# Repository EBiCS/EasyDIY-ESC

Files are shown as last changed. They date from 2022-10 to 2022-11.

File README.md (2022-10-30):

# EasyDIY ESC

Note: 'main' branch is under development, there is a change to use KiCad as compared to v0.5.2 (current HEAD of feature/v0_5_2, i.e. git SHA1 - e55e314)

The target for this EV motor controller is to power small EVs like EBikes or EScooters like Xiaomi M365, and offer better customizability and repairability.

## Main objectives:

* **Easy to build and repair DIY**: It uses DC-DC modules, a development board instead of an uC chip, SMD passive components are all 0805 or bigger, and ICs are SOIC8 or SOIC14. No fine pitch components.

* **Popular components:** Uses the popular Bluepill STM32F103 board, meaning it is easy to develop firmware for it. Uses popular components / footprints / pinouts. Meaning you should have no problems with part availability, and if you do, you will be able to change most parts with equivalents depending on availability or prefrence, without need to change the pcb layout.

* **Possible to add custom electronics:** For reusing this motor controller on different devices, you can extend the electrocnis with a custom header on top of the Bluepill. This means you can use all available pins and access and extend with: CAN, UARTs, etc.

* **Possibility to buy the SMD parts pre-soldered:** While we went to great extend do make this board easy to DIY by humans (as opposed to robots in a factory), we acknowledge there are many who lack the skill/time/motivation to solder all SMDs themselves. So all SMDs are on the same side, in large stock at lcsc (at the time of writing), so the board can be ordered with SMDs pre-assembled by JLCPCB for a decent price.

* **Compactness:** Despite using only big DIY friendly parts, we tried to keep the board as small as possible: ~ 73mm x 49mm

* **Good Power/Size ratio:** Our initial estimation (untested) is that the upper limit for phase current should be ~78A. As for max continuous “battery amps”, it heavily depends on the cooling!  

## ES Thread:
https://endless-sphere.com/forums/viewtopic.php?f=30&t=114537

## Building Tips:

### **Bus Bars**
Bus bars are recommended for anything else than very low current. (extra copper wires soldered to the exposed copper strips of the PCB, or at very least a lot of solder on the exposed strips)

### **Bulk electrolytic capacitors (XC.... )**
We went for a total of ~1000uF, which should be enough for most usecases. 
You need more capacitance the more power you plan to use, and the longer (and thinner) your battery wires are. So you can probably also get away with less if you have short thick battery wires.  
Choose voltage rating ~ 1.5x your max battery voltage for a long lifetime. For 48v nominal (54.6V max) battery voltage, 80V or more is recommended. 
The total capacitance of the electrolytic capacitors is more important than the exact combination of values. 1 big + 3 small is almost the same as 3 medium of the same total value. More smaller capacitors have the advantage of lower ESR, lower inductance, and redundancy in case one fails)

### **Bulk ceramic/MLC capacitors:  (XC.... )**
As much as possible. These need to compensate for the high frequency weakness of the electrolytic capacitors. Overrating voltage rating is recommended. (author chose 100V for the “default” for 3.3v, 5v and 12v). Definitely fill all open footprints. 

### **Capacitors - the rest**
Values are consolidated for easy buying. Voltage rating is 25V or higher regardless if they are on the 12v, 5v, or 3v3 rail on the default design, however you can choose a smaller voltage rating for the 5v and 3v3 rails..  
All parts are 0805 mlc (2 electrolytic exceptions, C8 and C10 from the 12v and 5v rails)

### **Snubbers (RSx, CSx)**
These are RC snubbers. **The current values for the R and C are random, they are here only for the footprints. Do not fit them (yet).** The real values (if necessary at all) will be computed after we build the controller and see what ringing we get. Purpose of the snubbers is to dampen that ringing. (if you choose different parts than the one we compute the snubbers for, you might need to compute the snubbers yourself). These components are not present in the pick-and-place or BOM files.

### **Optional Capacitors (OCx)**
All parts marked OCx are optional GS Capacitors for the mosfets. If you insist on using old/bad mosfets with high Crss, you'll need to compensate for that with additional Cgs. That being said, please avoid high Crss mosfets, and you don't need to use the OCx. We expect none of the recommended FETs to need these. These are footprints only to offer flexibility if needed. These components are not present in the pick-and-place or BOM files. 

### **FETs**
The default FETs are available from aliexpress at the time of writing. They are cheap and have good specs. (low Rds on, low Crss, 100v, etc). 
You can solder them “standing” on the the throughhole/module side, or bent flat on the opposite (smd) side. In either case, it is recommended that the thick part of the leads is in contact with (soldered to) the board. The thin part of the leads can carry significantly less current.

You can use a fet of your choosing, but please be aware that old Fets (such as the famous 4110 or 3077) have huge Crss, leading to a tiny Ciss/Crss ratio. This ratio needs to be bigger than roughly your max battery voltage, so you will need to compute and add the optional Cgs capacitors (OCx). Small Ciss/Crss results in ringing / parastic turn on (which leads to failure). 
That being said, it’s best to just use Fets with Ciss/Crss > ~100, nowadays they’re easy to find. See the spreadsheet with alternative parts. 

Attaching the FETs to a heatsink: the FETs need to be electrically isolated from the heatsink, but well connected thermally. The options for this are:
* Mica glass (“traditional option”, cheap, easy to find)
* Ceramics (saw this as a new option, never tried it)
* Polymer pads 
* Kapton Tape 

Unfortunately in focusing on making the board small we crammed the FETs very close together. This means some mica or ceramic pads will not fit - and it’s very hard to cut them afaik. So for this version we’re probably stuck with polymer / kapton. 

### **Testing**

* v0.5 build has been tested by mxlemming with MESC FOC firmware on F401CC black pill board

### **Known issues/limitations:**
* Mosfet temp sensor missing - you can add it to the expansion board. 
* Many connectors are not present (example: CAN)  - you can add them to the expansion board. 

## FAQ

* **What’s with those 2 solder jumpers?**
They are power for your uart-connected board. If it’s a 5v board, solder the 5v solder jumper, if it needs 3.3v solder the 3v3 jumper. Never solder both! 

* **Can you assemble it for me?**
You can get the SMD side pre-assembled at jlcpcb (at the time of design all parts were in stock for jlcpcb SMT service). So you’ll only need to solder the through-hole parts and the modules. Currently there is no plan on selling any assembled PCBs.

* **I want more power!!!**
This might not go well. So good luck, you’ll probably need it. Please don't blame us when it goes up in smoke. But do let us know how it goes. Disclamer aside, here are some basic suggestions:
   * Stack another 1mohm shunt on top of the other. This will double the max current you can read. 
   * Add thick bus bars to the board.
   * Add more/ bigger bulk caps!
   * Use appropriate wires (thick!) 

* **I want more voltage!!!!**
Realistic limit is 15s lipo. For more than that the ESC will need serious redesign.
Some bottlenecks that cross my mind: 
   * default 12v dc module is 72v limited, 
   * some of the recommended mosfets are not capable of more voltage, 
   * voltage sense divider needs adjustment, etc. 
   * PS: I would have loved to make it 20s capable, but did not find any small 100-12v DC-DC module. If you know of one, please let us know in our ES thread, and next version might be 20s / 74v capable. Also, I added 3 through hole pads for easy mounting of any 12V module via wires :)

* **Your part X is bad, I recommend Y!**
We tried to find cheap but decent parts for this controller. Cheap almost always implies a compromise in some other areas, so you might not like our pick :)
It should be fairly easy to switch to other parts on your own: we used mostly standard and popular footprints and packages
If you know better parts or have better solutions, please let us know on our ES thread. We like learning new things. 
....except if you’re going to suggest 3077 or 4110 mosfets. Those things are dinosaurs. They were the biggest baddest thing around during their time, but nowadays belong to a museum. Or a kid’s t-shirt. Please stop recommending them. See our thread for details.

* **Where can I buy parts?**
Lcsc.com, mouser.com. Aliexpress if needed. 
I designed this with jlcpcb smt assembly in mind, so all SMDs were in stock at lcsc when I designed the PCB. Also most of the Through-hole parts. 
Some exceptions, and where to buy them:
   * Default mosfets - aliexpress. 
   * 12v module - mouser
   * 5v module - aliexpress. There is a fixed voltage one, we recommend that one! 
   * Bluepill - aliexpress. Don’t know a better source these days. 
   * Jst headers - aliexpress
   * Bluepill headers - aliexpress

* **Why do the battery wires go in seemingly random places in the middle of the board?**
If you have the battery wires at the edge, then the full battery current will need to go through a portion of the battery “traces” of the PCB. I’ve placed them near the middle switch node, so with a tiny exception, the current through the traces is ⅓ of the battery current. 

* **This whole thing is amateur work!**
Yeah, totally true. We are amateurs working on a generic low power ESC for free. If by this you refer to any specific mistake / set of mistakes, we would love to know about it! Post in the ES thread. Thanks!

## Change log v0.5 -> v0.5.2

### Schematic
* Changes:
  * changed voltage sense resistors to 10x lower value (basic jlcpcb resistors -> cheaper)
  * removed pin 20 from GND (for blackpill compatibility)
  * removed thermal reliefs
  * replaced some parts with more cost-effective equivalents (basic parts jlcpcb)
  * changed diodes to a bigger more rugged version (more inline with the philosophy of this controller)
  * changed voltage sense divider so max read voltage is 100V (20s compatibility)
  * added circuitry for a ntc temp sensor for mosfets.
  * changed the electrolytic caps from the 12V and 5V rails to MLCC (still more capacitance than manufacturer recommends)
  * swapped ntc pins: MOSFET Temp -> A0, and Motor Temp -> A1 (for compatibility with EBiCS v2)
  * changed pinout of HALL JST connector - now you can use, additionally to a 6 pin connector for motors with temp NTC sensor, a 5pin connector on pins 1-5 and it will directly be compatible with the cable of a motor without temp sensor (M365 would be a popular example)
### PCB Design 
  * added 3 through hole pads for vbat, 12v, and gnd for easy connection with wires of any dc-dc module for more flexibility
  * moved JST connectors away from bluepill for better fitting (increased board width by 1mm)
  * many minor layout changes 

## Change log v0.1 -> v0.5

### Schematic
* Fixes:
  * added voltage divider for the voltage follower op-amp
  * added connection between the 3 2k2 resistors and 3V3 on hall sensor inputs
  * changed decoupling caps of the 3 power stages from VBAT-Shunt to VBAT-GND 

* Changes
  * replaced "default" mosfets with much better model
  * replaced shunts with 1mOhm (much lower value)
  * connected bluepill pin 20 to GND
  * changed the RC from the phase wire of the power stages to snubbers
  * replaced opamp with better model
  * changed Opamp 2 to be the voltage follower for easier routing
  * replaced vattery connectors with 2 pads for wire soldering
  * removed one of the connectors for hall sensors, replaced the other one with JST PH. 
  * pinout changes for leaving CAN pins free
  * replaced mini 360 with MP1584EN (is bigger, but there is a non-adjustable 5V version, which is less error-prone to use.)
  * changed all ceramic decoupling capacitors for 3v3 and 5v to 10uF 0805
  * changed all bootstrap capacitors to  10uF 0805
  * added 1 ceramic decoupling capacitor per power stage (for a total of 2) 
  * increased gain of opamps to 10 (from 8)
  * consolidated pullup R values to 2k2
  * consolidated many other C and R values
  * removed diode and cap from the hall sensor 5v rail
  * removed extension board headers (will be mounted on top of the bluepill on the same pins)
  * replaced electrolytic caps with bigger values and bigger voltage ratings

### PCB design:

* Fixes: 
  * Moved the decoupling capacitor close to the bus bars (GND was through a long thin trace which rendered it almost useless) 	

* Changes:
  * moved to 4 layer board (Ground Planes rule!)
  * moved the opamp non-inverting input resistors near the shunt - so they get the potential of that local ground (not of the GND near the opamp) 
  * stacked DC-DC modules
  * removed expansion board headers
  * added 3 JST PH headers for basic functions
  * moved vbat rail at the edge of the board and GND rail in the middle
  * major redesign of everything
  * greatly reduced the size

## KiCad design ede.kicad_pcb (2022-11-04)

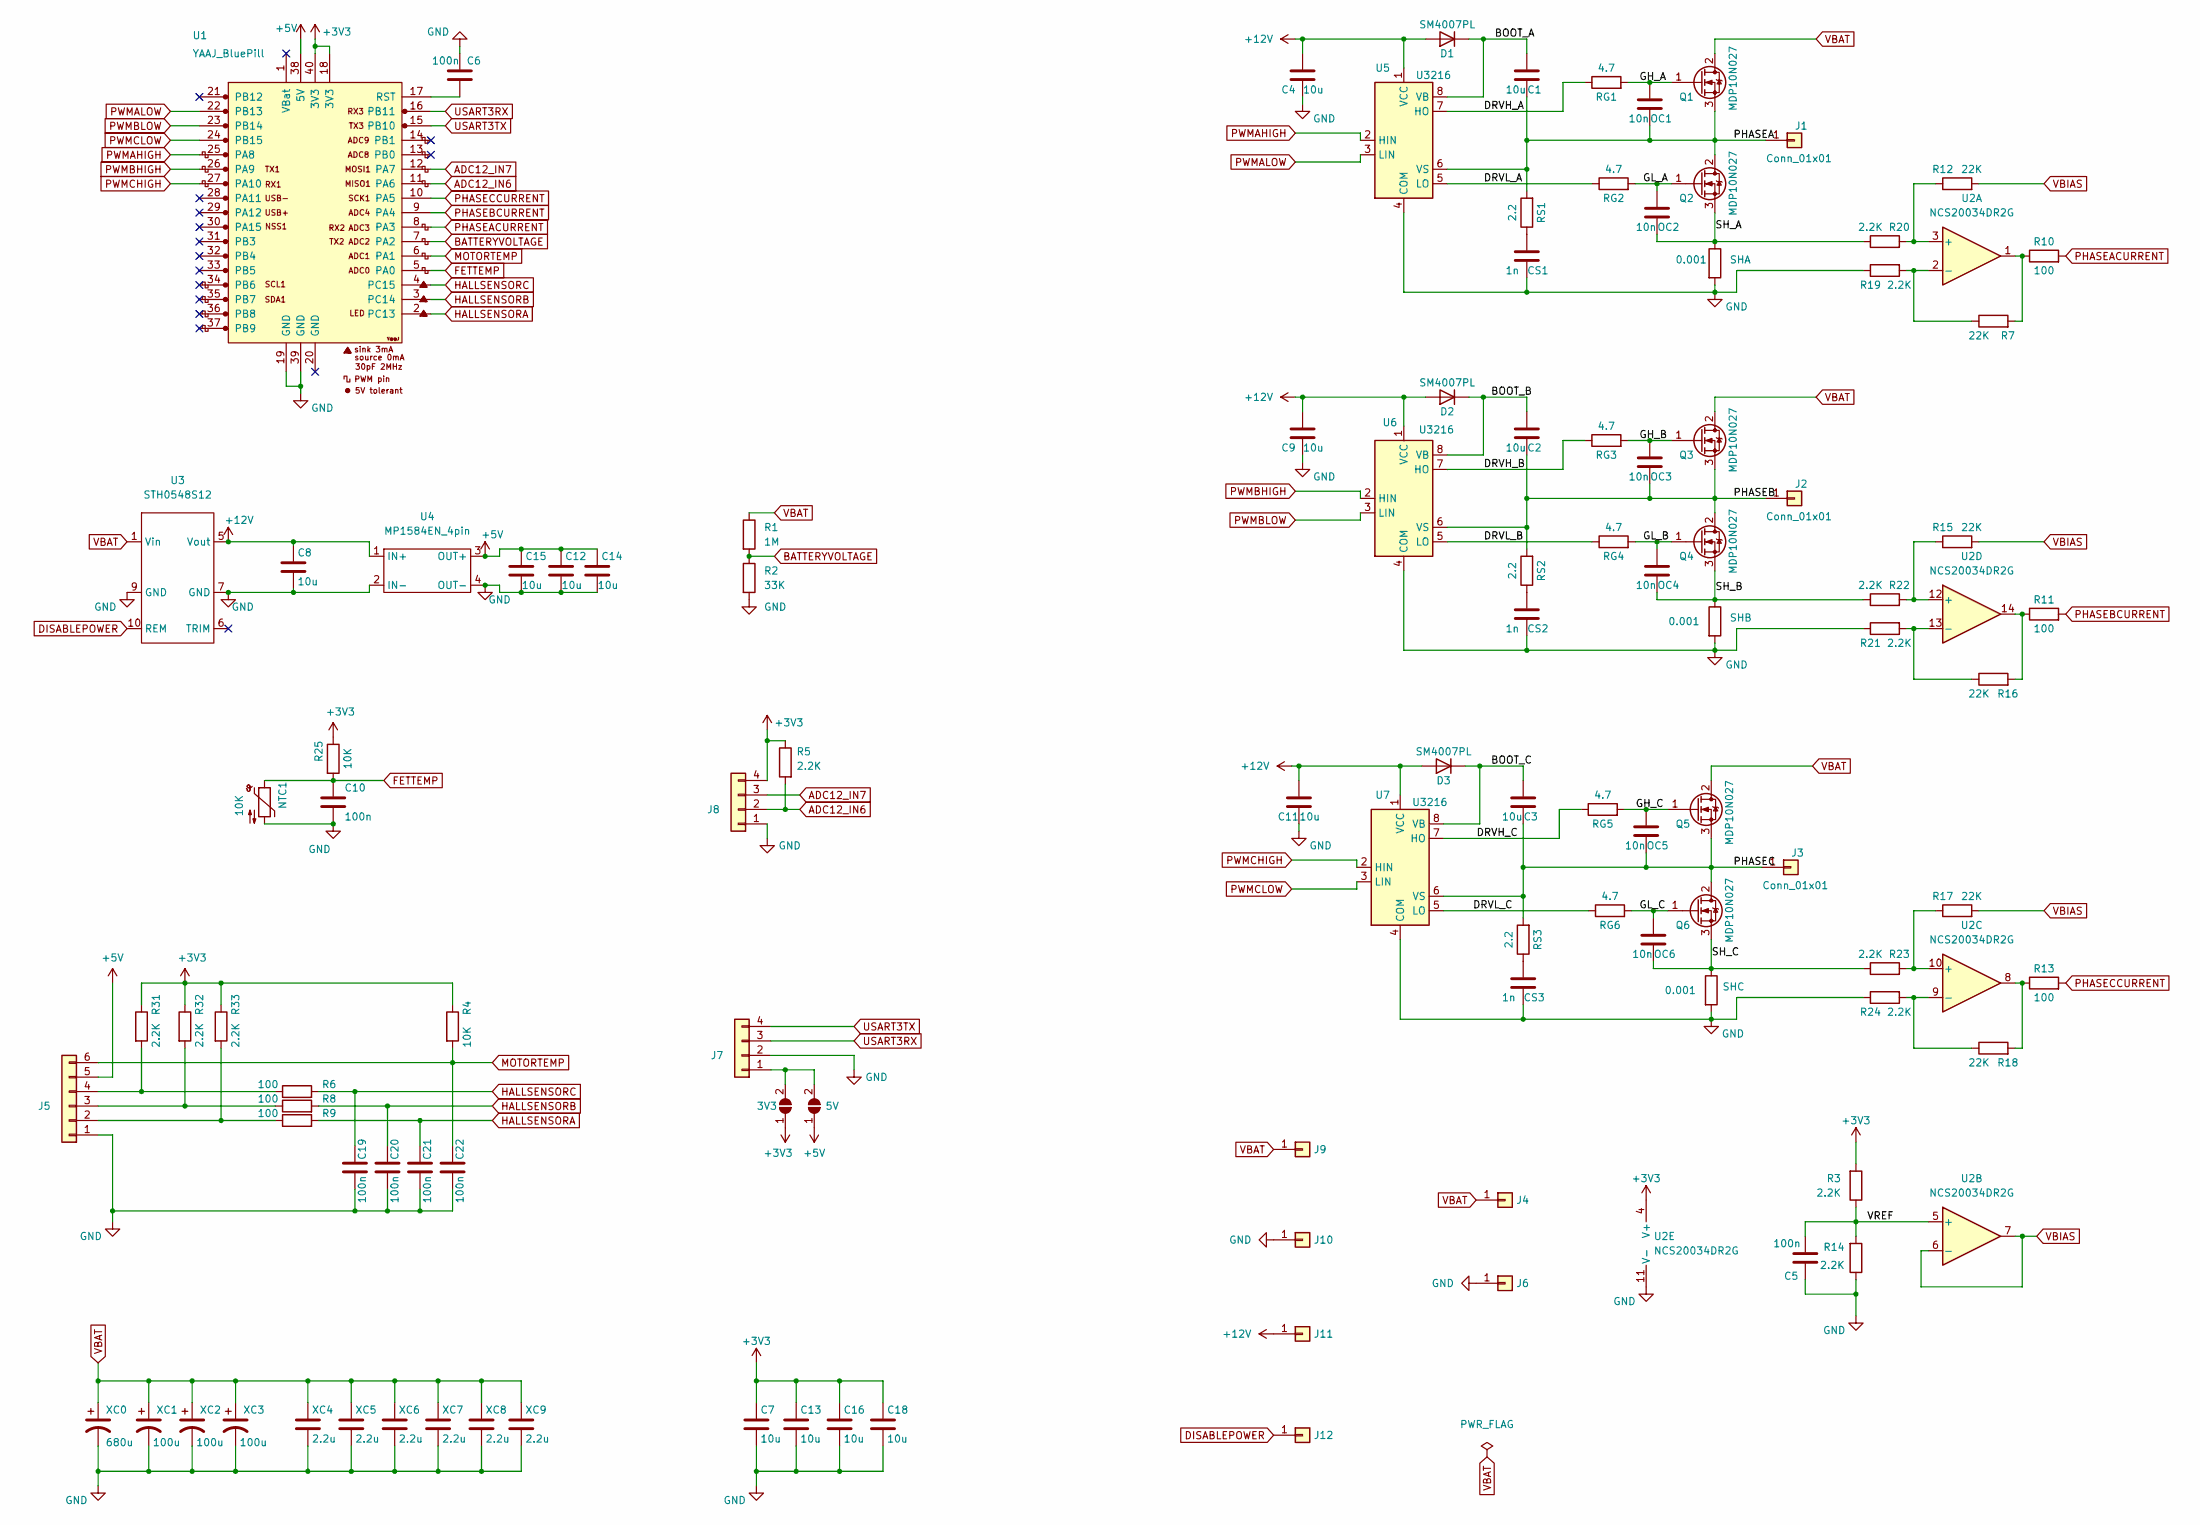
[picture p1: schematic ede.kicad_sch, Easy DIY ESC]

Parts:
C1, C2, C3, C4, C7, C8, C9, C11, C12, C13, C14, C15, C16, C18: 10u; C_0805_2012Metric_EDE
C5, C6, C10, C19, C20, C21, C22: 100n; C_0805_2012Metric_EDE
CS1, CS2, CS3: 1n; C_0805_2012Metric_EDE
D1, D2, D3: SM4007PL; D_SOD-123_EDE
J1, J2, J3, J4, J6: Conn_01x01; THT_1x_ID_2.8_OD_4
J5: Conn_01x06; JST_PH_B6B-PH-K_1x06_P2.00mm_Vertical_EDE
J7, J8: Conn_01x04; JST_PH_B4B-PH-K_1x04_P2.00mm_Vertical_EDE
J9, J10, J11: Conn_01x01; THT_1x_ID_1_OD_2
J12: Conn_01x01; TestPoint_Pad_D1.4mm_EDE
JP1, JP2: SolderJumper_2_Open; SolderJumper-2_small_EDE
NTC1: 10K; THT_2x_P2.54_ID_0.7_OD_1.3
OC1, OC2, OC3, OC4, OC5, OC6: 10n; C_0805_2012Metric_EDE
Q1, Q2, Q3, Q4, Q5, Q6: MDP10N027; TO-220-3_Vertical_EDE
R1: 1M; R_0805_2012Metric_EDE
R2: 33K; R_0805_2012Metric_EDE
R3, R5, R14, R19, R20, R21, R22, R23, R24, R31, R32, R33: 2.2K; R_0805_2012Metric_EDE
R4, R25: 10K; R_0805_2012Metric_EDE
R6, R8, R9, R10, R11, R13: 100; R_0805_2012Metric_EDE
R7, R12, R15, R16, R17, R18: 22K; R_0805_2012Metric_EDE
RG1, RG2, RG3, RG4, RG5, RG6: 4.7; R_0805_2012Metric_EDE
RS1, RS2, RS3: 2.2; R_0805_2012Metric_EDE
SH1, SH2, SH3: 0.001; R_2512_6332Metric_EDE
U1: YAAJ_BluePill; YAAJ_Bluepill
U2: NCS20034DR2G; SOIC-14_3.9x8.7mm_P1.27mm_EDE
U3: STH0548S12
U4: MP1584EN_4pin
U5, U6, U7: U3216; SOIC-8_3.9x4.9mm_P1.27mm_EDE
XC0: 680u; CP_Radial_D12.5mm_P5.00mm_EDE
XC1, XC2, XC3: 100u; CP_Radial_D8.0mm_P3.50mm_EDE
XC4, XC5, XC6, XC7, XC8, XC9: 2.2u; C_1206_3216Metric_EDE

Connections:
+3V3: C7.1, C13.1, C16.1, C18.1, J8.4, JP1.1 (A), R3.2, R4.1, R5.1, R25.1, R31.1, R32.1, R33.1, U1.18 (3V3), U1.40 (3V3), U2.4 (V+)
+5V: C12.1, C14.1, C15.1, J5.5, JP2.1 (A), U1.38 (5V), U4.3 (OUT+)
+12V: C4.1, C8.1, C9.1, C11.1, D1.2 (A), D2.2 (A), D3.2 (A), J11.1, U3.5 (Vout), U4.1 (IN+), U5.1 (VCC), U6.1 (VCC), U7.1 (VCC)
/BOOT_A: C1.1, D1.1 (K), U5.8 (VB)
/BOOT_B: C2.1, D2.1 (K), U6.8 (VB)
/BOOT_C: C3.1, D3.1 (K), U7.8 (VB)
/DRVH_A: RG1.1, U5.7 (HO)
/DRVH_B: RG3.1, U6.7 (HO)
/DRVH_C: RG5.1, U7.7 (HO)
/DRVL_A: RG2.1, U5.5 (LO)
/DRVL_B: RG4.1, U6.5 (LO)
/DRVL_C: RG6.1, U7.5 (LO)
/GH_A: OC1.1, Q1.1 (G), RG1.2
/GH_B: OC3.1, Q3.1 (G), RG3.2
/GH_C: OC5.1, Q5.1 (G), RG5.2
/GL_A: OC2.1, Q2.1 (G), RG2.2
/GL_B: OC4.1, Q4.1 (G), RG4.2
/GL_C: OC6.1, Q6.1 (G), RG6.2
/PHASEA: C1.2, J1.1, OC1.2, Q1.3 (S), Q2.2 (D), RS1.2, U5.6 (VS)
/PHASEB: C2.2, J2.1, OC3.2, Q3.3 (S), Q4.2 (D), RS2.2, U6.6 (VS)
/PHASEC: C3.2, J3.1, OC5.2, Q5.3 (S), Q6.2 (D), RS3.2, U7.6 (VS)
/SH_A: OC2.2, Q2.3 (S), R20.1, SH1.1
/SH_B: OC4.2, Q4.3 (S), R22.1, SH2.1
/SH_C: OC6.2, Q6.3 (S), R23.1, SH3.1
/VREF: C5.2, R3.1, R14.2, U2.5 (+)
ADC12_IN6: J8.2, R5.2, U1.11 (PA6)
ADC12_IN7: J8.3, U1.12 (PA7)
BATTERYVOLTAGE: R1.2, R2.1, U1.7 (PA2)
DISABLEPOWER: J12.1, U3.10 (REM)
FETTEMP: C10.1, NTC1.1, R25.2, U1.5 (PA0)
GND: C4.2, C5.1, C6.2, C7.2, C8.2, C9.2, C10.2, C11.2, C12.2, C13.2, C14.2, C15.2, C16.2, C18.2, C19.2, C20.2, C21.2, C22.2, CS1.2, CS2.2, CS3.2, J5.1, J6.1, J7.2, J8.1, J10.1, NTC1.2, R2.2, R14.1, R19.1, R21.1, R24.1, SH1.2, SH2.2, SH3.2, U1.19 (GND), U1.39 (GND), U2.11 (V-), U3.7 (GND), U3.9 (GND), U4.2 (IN-), U4.4 (OUT-), U5.4 (COM), U6.4 (COM), U7.4 (COM), XC0.2, XC1.2, XC2.2, XC3.2, XC4.2, XC5.2, XC6.2, XC7.2, XC8.2, XC9.2
HALLSENSORA: C21.1, R9.2, U1.2 (PC13)
HALLSENSORB: C20.1, R8.2, U1.3 (PC14)
HALLSENSORC: C19.1, R6.2, U1.4 (PC15)
MOTORTEMP: C22.1, J5.6, R4.2, U1.6 (PA1)
unnamed: C6.1, U1.17 (RST)
unnamed: CS1.1, RS1.1
unnamed: CS2.1, RS2.1
unnamed: CS3.1, RS3.1
unnamed: J5.2, R9.1, R33.2
unnamed: J5.3, R8.1, R32.2
unnamed: J5.4, R6.1, R31.2
unnamed: J7.1, JP1.2 (B), JP2.2 (B)
unnamed: R7.2, R10.1, U2.1
unnamed: R11.1, R16.2, U2.14
unnamed: R12.1, R20.2, U2.3 (+)
unnamed: R13.1, R18.2, U2.8
unnamed: R15.1, R22.2, U2.12 (+)
unnamed: R16.1, R21.2, U2.13 (-)
unnamed: R17.1, R23.2, U2.10 (+)
unnamed: R18.1, R24.2, U2.9 (-)
unnamed: R7.1, R19.2, U2.2 (-)
PHASEACURRENT: R10.2, U1.8 (PA3)
PHASEBCURRENT: R11.2, U1.9 (PA4)
PHASECCURRENT: R13.2, U1.10 (PA5)
PWMAHIGH: U1.25 (PA8), U5.2 (HIN)
PWMALOW: U1.22 (PB13), U5.3 (LIN)
PWMBHIGH: U1.26 (PA9), U6.2 (HIN)
PWMBLOW: U1.23 (PB14), U6.3 (LIN)
PWMCHIGH: U1.27 (PA10), U7.2 (HIN)
PWMCLOW: U1.24 (PB15), U7.3 (LIN)
USART3RX: J7.3, U1.16 (PB11)
USART3TX: J7.4, U1.15 (PB10)
VBAT: J4.1, J9.1, Q1.2 (D), Q3.2 (D), Q5.2 (D), R1.1, U3.1 (Vin), XC0.1, XC1.1, XC2.1, XC3.1, XC4.1, XC5.1, XC6.1, XC7.1, XC8.1, XC9.1
VBIAS: R12.2, R15.2, R17.2, U2.6 (-), U2.7

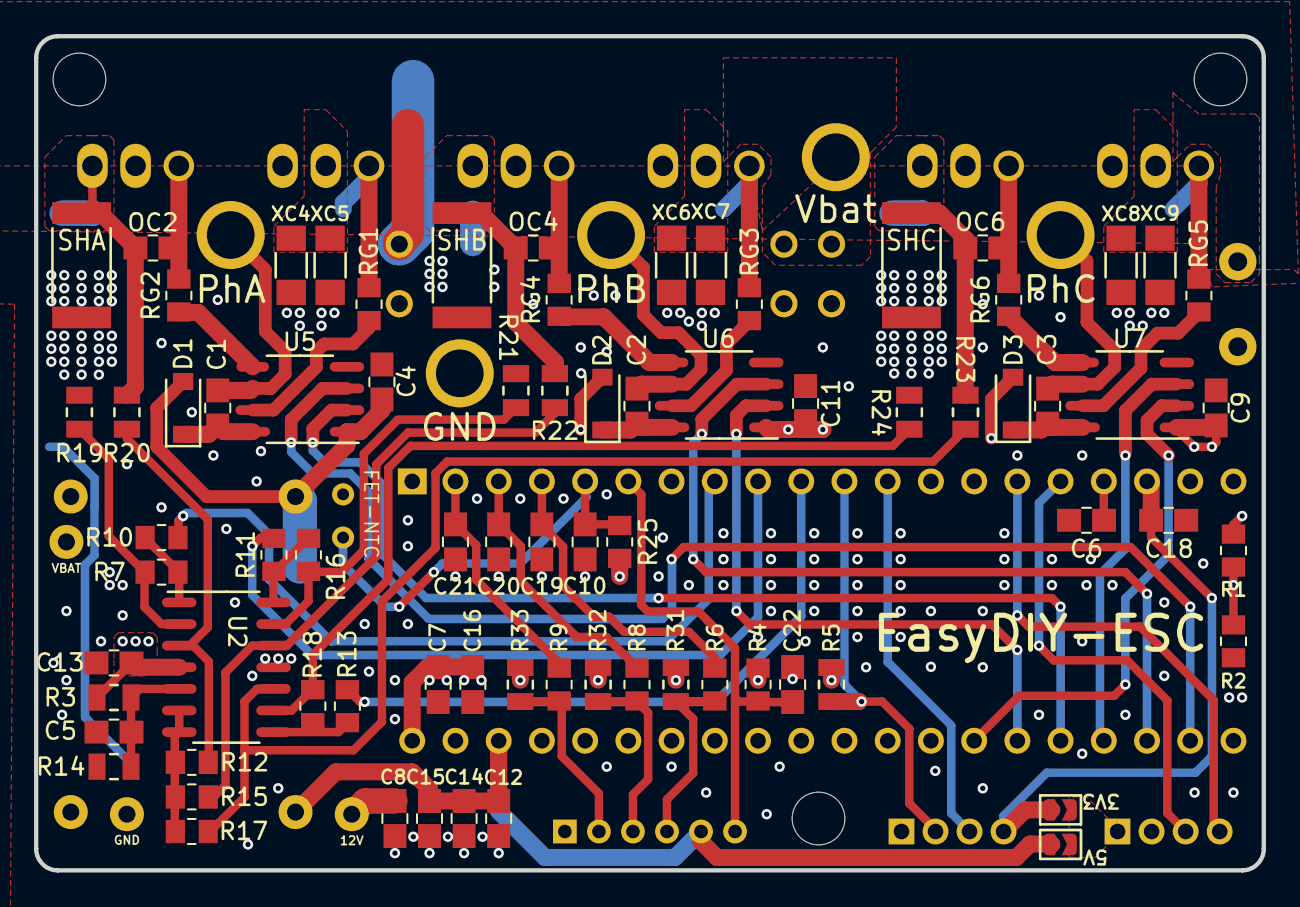
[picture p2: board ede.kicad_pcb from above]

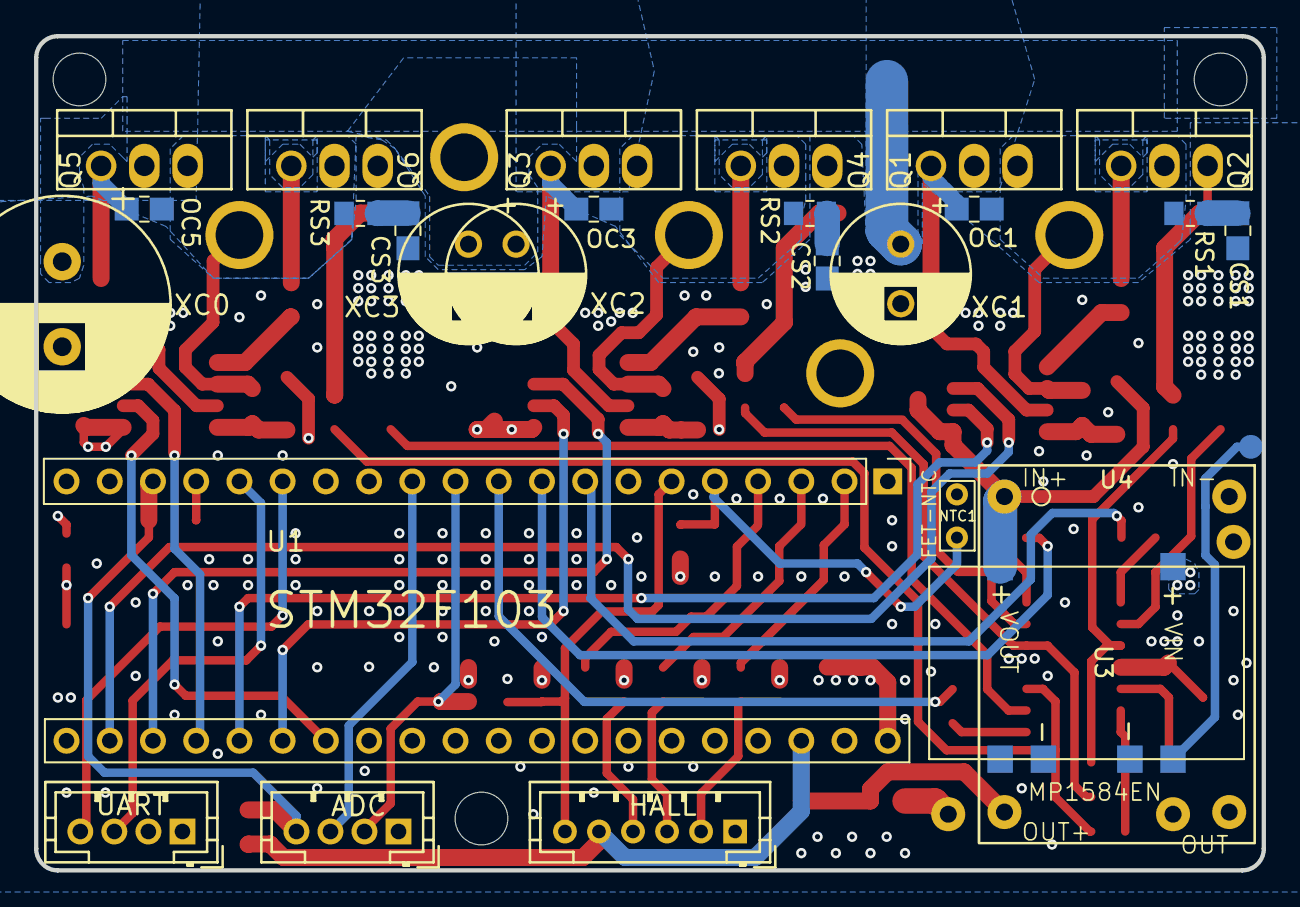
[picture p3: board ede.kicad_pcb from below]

Board: 4 copper layers, 72.1 x 49.0 mm, 111 parts (27 on the bottom side), 65 nets.

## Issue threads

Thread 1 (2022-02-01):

Two motors with one STM32 microcontroller?

happytm, 2022-02-01:
Is it possible to run 2 motors with one STM32 micro controller by adding 6 more mosfets?
Are there enough pin available?

Thanks.

runger1101001, 2022-02-01:
Yes, it is possible!

- If you want 2 x 6-PWM control you need a model with two advanced control timers, normally TIM1 and TIM8.
- It has to be a fairly fast MCU to run 2 times the SimpleFOC loop
- if you want current sensing, you will need 6 ADC pins also
- and you need 2 sensor inputs, for ABI you would ideally use 2 more timers and our [STM32HardwareEncoder](https://github.com/simplefoc/Arduino-FOC-drivers/tree/master/src/encoders/stm32hwencoder) or use SPI, maybe with two separate SPI buses...

I think most of the STM32G4 series would be suitable.

Here is an example design I made, with 2x 6-PWM, 2x current sensing and 2x SPI bus for sensors:
https://github.com/rosmo-robot/Rosmo_ESC

runger1101001, 2022-02-01:
(but it is not possible using a BluePill or BlackPill MCU board - not enough pins; but I guess one of the big Nucleo boards could do it...)

happytm, 2022-02-03:
Thank you @runger1101001 for your insight.

happytm, 2022-02-08:
@runger1101001 How about using ESP32 ? Does it have enough pins to run 2 motors?

Thanks.

runger1101001, 2022-02-08:
Pins are always in short supply on the ESP32! It only has relatively few to begin with compared to other MCUs, and then they are so complicated to use... some are input only, some can't be used at the same time as WiFi, and some are only "pretend" pins since they're actually connected to the flash memory can you can't use them at all...

So the answer is: it depends.
A DevKit type MCU-board: not really, I don't think so.
A ESP32 module or chip with 2x 3-PWM driver: I think it is possible.
A ESP32 module or chip with 2x 6-PWM driver and 2x current sense: not sure, but probably.

happytm, 2022-02-09:
I think the middle option (A ESP32 module or chip with 2x 3-PWM driver: I think it is possible) seems attractive option for low cost motor controller. I wanted a low cost controller to control 2 250 watts hoverboard motors for my project using SimpleFoc.

Your https://github.com/rosmo-robot/Rosmo_ESC project looks promising if it can use ESP32 and at least 10A drivers and Mosfets.

Thanks.

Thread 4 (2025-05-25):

About Back EMF

TheSnowFall, 2025-05-25:
How does this design protect against Back EMF from BLDC phases?

runger1101001, 2025-05-25:
It doesn’t… the BEMF current goes back in your battery…

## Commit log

2022-10-12 EasyDIY-ESC KiCad adaptation
    [ede.kicad_pcb, ede.kicad_sch]
2022-10-12 sch, pcb: add date
    [ede.kicad_pcb, ede.kicad_sch]
2022-10-12 pcb: B.Cu & In2.Cu fix
    [ede.kicad_pcb]
2022-10-13 pcb: Mask for busbars & phase connectors
    [ede.kicad_pcb]
2022-10-15 pcb: avoid sharp edges
    [ede.kicad_pcb]
2022-10-15 README: rough update to the current state
2022-11-04 pcb : uncheck 'include netlist attributes'
    To be on par with JLCPCB recommended setting.
    Though extended X2 format is not in recommended settings, since it is mentioned
    don't care in JLCPCB docs, it has been enabled.
    [ede.kicad_pcb]
2022-11-04 pcb: use drill/place file origin
    To compare easily with v0.5.2 gerbers
    [ede.kicad_pcb]
2022-11-04 submodule: C0805 fix & R0805 small footprint
2022-11-04 pcb: integrate C0805 library pad dimension swap
    [ede.kicad_pcb]
2022-11-04 pcb: alter some of the R0805 footprint as per reference
    [ede.kicad_pcb]
2022-11-04 pcb: fix DRC clearance violation error
    [ede.kicad_pcb]
2022-11-04 pcb: avoid more bends on Ph C driver to bypass cap route
    [ede.kicad_pcb]
2022-11-04 pcb: alter R0805 footprints on B.Cu as per reference
    [ede.kicad_pcb]
2022-11-04 pcb: bring In2.Cu +12V busbar more similar to v0.5.2
    [ede.kicad_pcb]
2022-11-04 pcb: In2.Cu gnd zone continuous b/n FET legs
    zone minimum width reduced to 0.2
    [ede.kicad_pcb]
2022-11-04 pcb: T.Cu Mtr temp resistor 3.3V via to track improvement
    [ede.kicad_pcb]
